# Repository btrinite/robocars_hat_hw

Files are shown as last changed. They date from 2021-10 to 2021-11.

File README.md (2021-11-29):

# This repository contains the hardware part of the DIYRobocarsFr Hat.

## Intro
This Hat is designed for Raspberry Pi 3/4, Jetson Nano or any other SBC implementing the well known 'rpi' GPIO connector.
This Hat provides various interfaces between SBC (Single Board Controler) and hardware to easely build an autonomous small scale RC-style car.
A typical example of such build is the [Donkey car](https://www.donkeycar.com/)

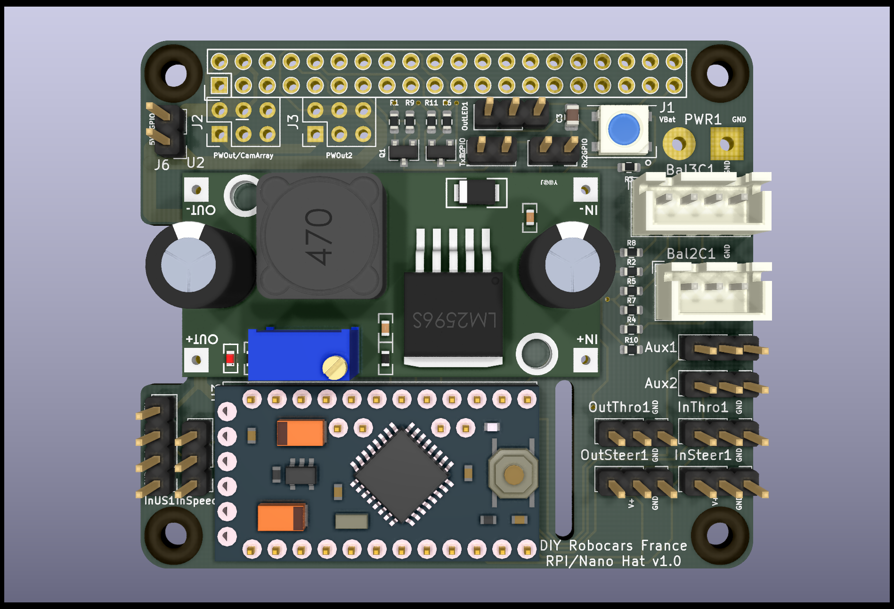
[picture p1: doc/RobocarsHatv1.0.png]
DIY Robocars FR Hat


The Hat combines :
- LM2596 or xl4005 DSN5000 based DC/DC converter to power everything from a single battery (7-15V, NiMh or LiPo 2S/3S), through GPIO or through dedicated connector.
- Arduino pro mini 5V 16Mhz, which drive I/O (PWM Inpput/output, Ultrasonic sensor, RPM sensor, ...). 5V version is prefered since most of the sensors works at 5v.
- Serial communication link between Arduino and SBC through GPIO pin 8 and 10, with level shift 5v/3.3V 
- Tension divider bridge for Battery monitoring
- RBG Led to display status
- compatibility (stackable) with Arducam CamArray

The Hat has the following I/O :
- 40 pin header GPIO compatible with Raspberry PI and Nvidia Jetson with UART0 wired to the arduino through level shift
- 3 Battery power in connectors (2 wires, 3 wires or 4 wires)
- 2 PWM Inputss to connect RC Receiver (Throttle and Steering input)
- 2 PWM Outputs to connect drive train (ESC and Servo, for Throttle and Steering output) 
- 2 PWM Aux Inputs/Outputs
- 1 input for RPM sensor
- 1 input for UltraSOund sensor
- Aux connector for additional power output (5V and 3.3V) and to stack ArduCam CamArray
- WS2812B compatible output to control more RGB Led

The follwing jumpers are provided for convenience :
- 5V to GPIO : to inject 5V power supply to the Host through GPIO connector (to power Raspberry or Jetson Nano from the main Battery).
For other Hosts, please check documentation
- UART0 RX/TX Jumper : Usually, you need those jumpers since all communication between Host and Hat goes through this UART. Removing those jumpers could be needed to isolate Arduino UART while re-flashing it (especially if Host is powered on at flahsing time).

## Wiring
A typical wiring of the Hat is shown below : 

Hat Wiring

## Schematic

Consult [Schematics.pdf](doc/Schematics.pdf)

## Note on PWM Block

### Power supply
Hat does not provide power supply through PWM Inputs/Outpus. It is usualy duty of the motor controller (ESC) which feature a BEC.
This is to avoid mixing logic and actuators on the same power source. It means that as long as ESC is not connected and switchded on, Servo and RX Receiver will not be powered.

### output Idle signal
In the current implementation,

- First, as soon as the Hat is powered, a default Idle signal is driven (1,5ms pulse width)
This default idle signal could differ from the one you could have when doing calibration. 

- Second, many ESC will autocalibrate to this idle signal at startup time (when switched on) 

If you are in that case, it is recommanded to switch on the ESC only after the main application is up and running.

## Dependencies

Third party components libraries needed :

* [LM2596 DC to DC buck/step-down module](https://github.com/yet-another-average-joe/KiCad-Chinese_Modules/tree/main/DCDC_StepDown_LM2596)

* https://github.com/g200kg/kicad-lib-arduino.git

## Firmware

### Source
Firmware to upload to the Arduino ca be found [here](https://github.com/btrinite/robocars_hat)

### Flash firmware
To flash firmware, you need to connect a 5V FTDI adaptor featuring DTR signal and use Arduino IDE to flash/upload the content.
Do not forget to solder Pin header connector on Arduino Pins dedicated for uploading/flash purpose.
You can find more informations [here](https://www.arduino.cc/en/Guide/ArduinoProMini)

## Troubleshooting

### Loopback test (only applicable when using SimpleSerial protocol version of the firmware)
SimpleSerial protocol messages that carry throttle and steering are almost symetrical. Thus, if you loopback the serial comunication (RX wired to TX), the Hat will
work in loopback mode. Throttle/Steering orders received from RX Receiver will be used to drive Throttle/Steering output.

Loopback mode is achieved by :
- removing Rx/Tx jumpers to decouple UART signal from Host
- Wiring Rx and Tx together

This is illsutrated below : 

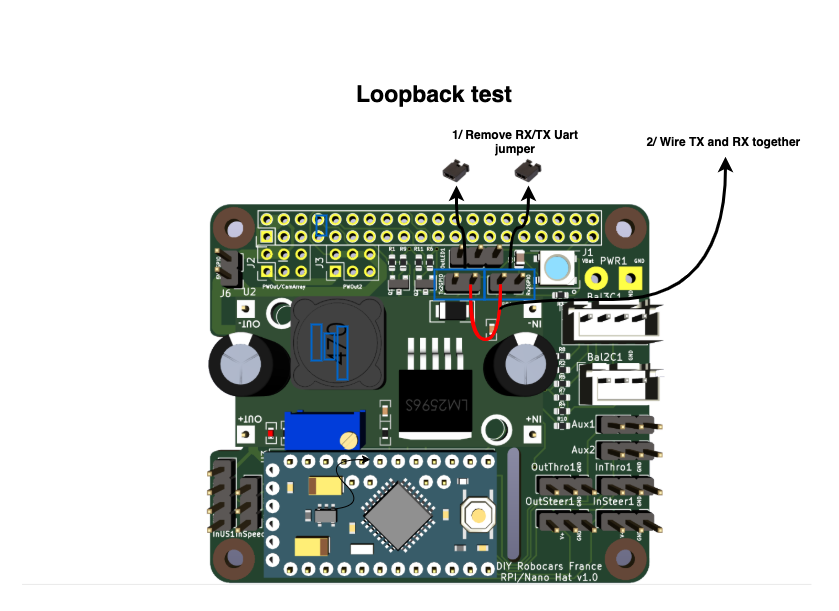
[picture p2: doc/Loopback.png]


## Example of integration
Modified Donkeycar software with integration of the DIYRobocarsFr Hat is available [here](https://github.com/btrinite/donkey_with_robocars_hat)

## Credits
Based on https://github.com/devbisme/RPi_Hat_Template

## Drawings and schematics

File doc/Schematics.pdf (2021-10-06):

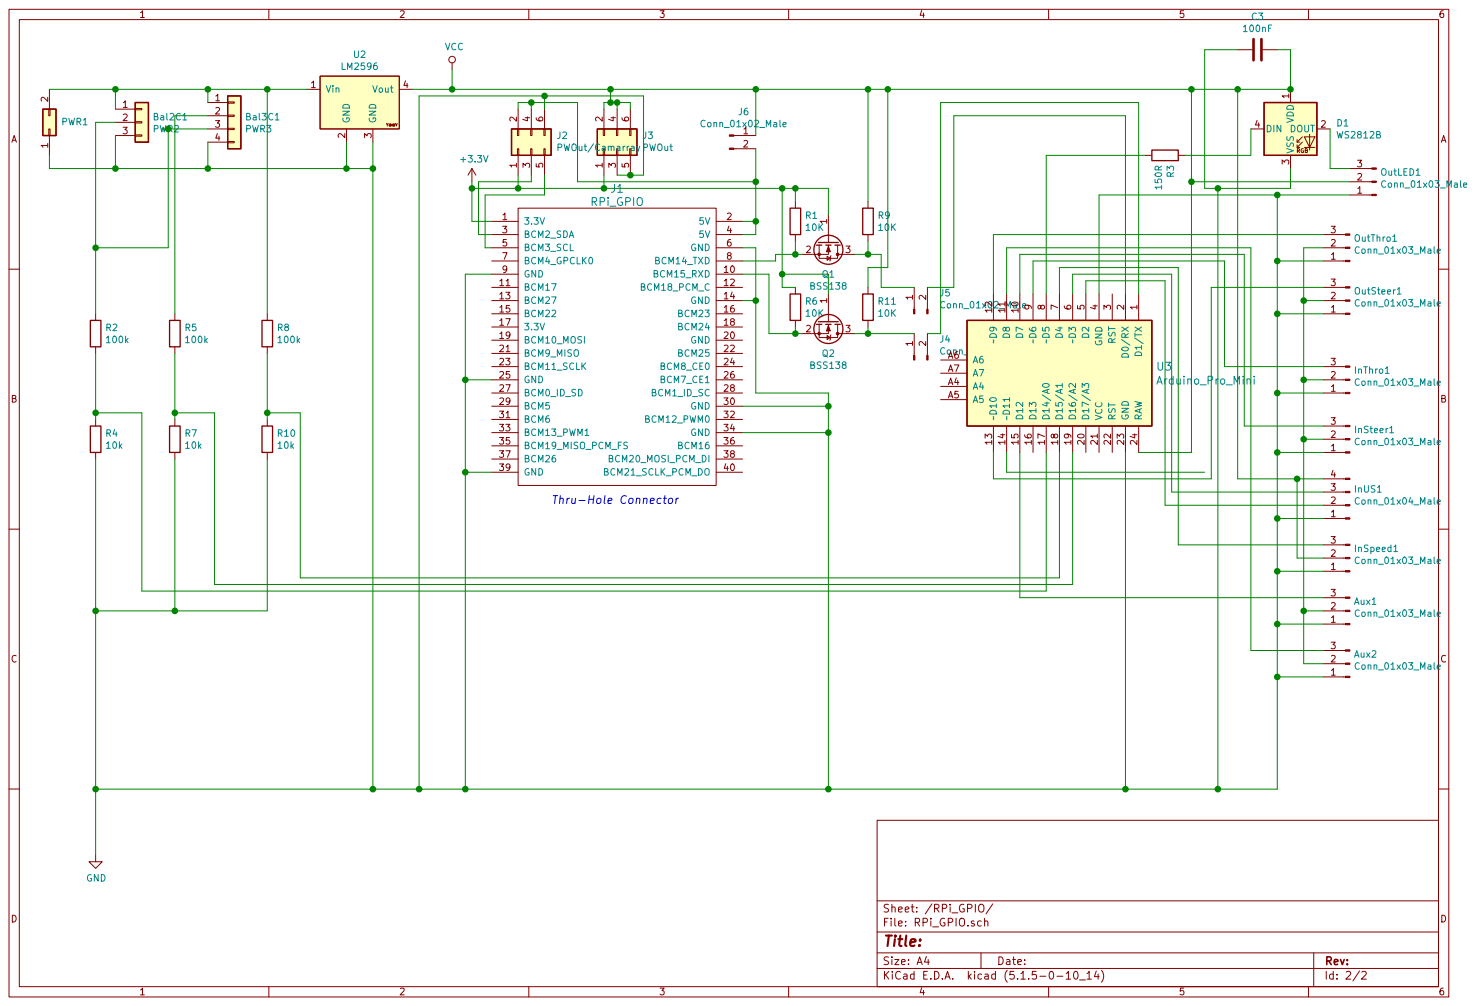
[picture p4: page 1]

2 D17/A3 20 VCC 21 RST 22 GND 23 RAW 24 RST

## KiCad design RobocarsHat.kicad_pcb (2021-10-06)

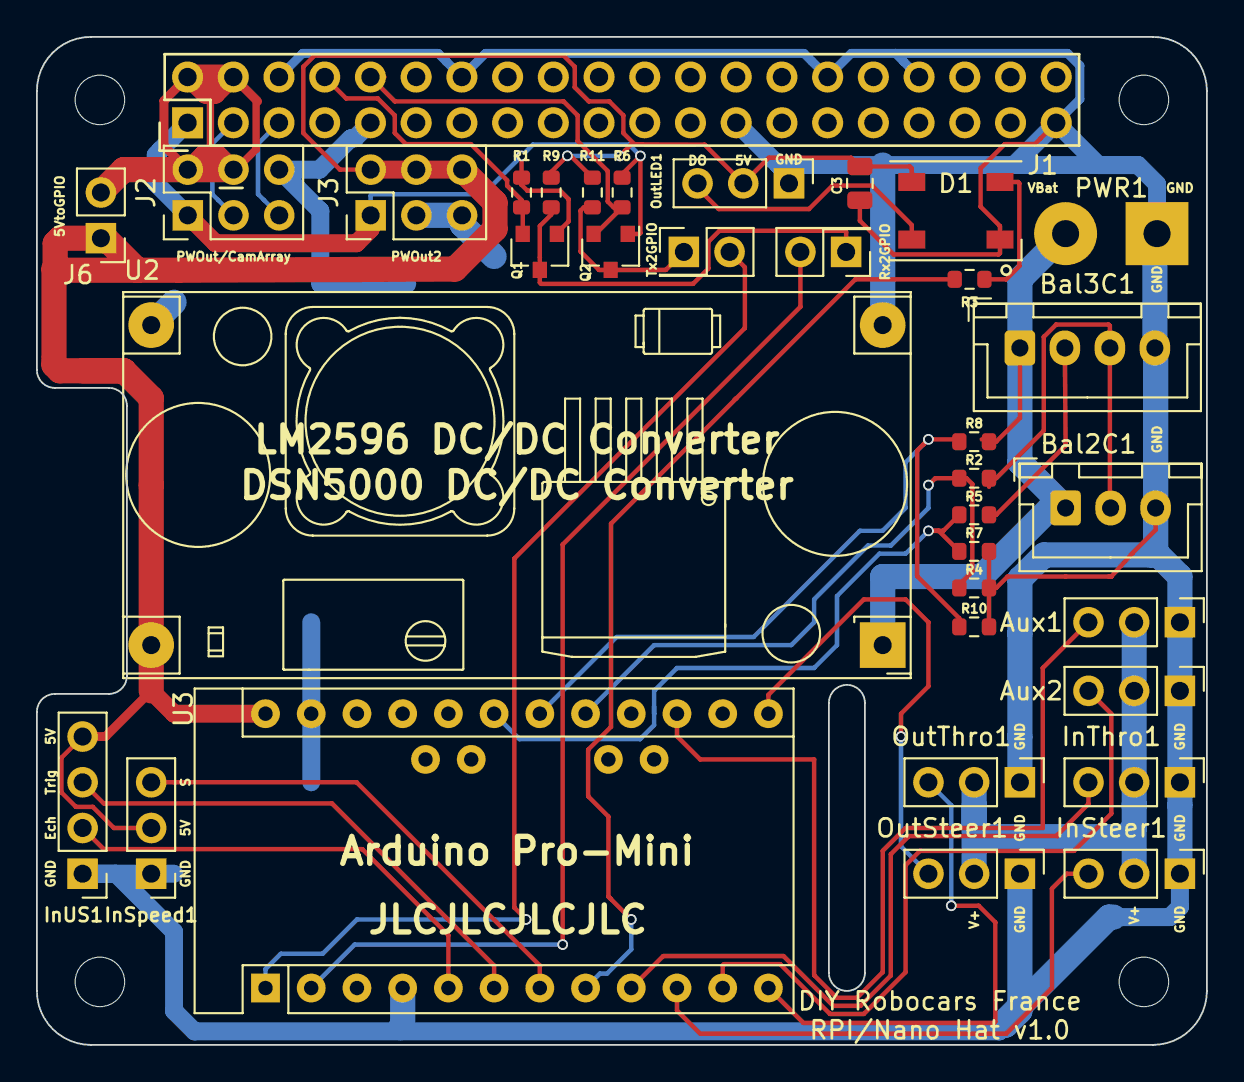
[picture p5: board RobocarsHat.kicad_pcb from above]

Board: 2 copper layers, 65.0 x 56.0 mm, 35 parts (0 on the bottom side), 31 nets.

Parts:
Aux1, Aux2: Conn_01x03_Male; PinHeader_1x03_P2.54mm_Vertical
Bal2C1: PWR2; JST_XH_B3B-XH-A_1x03_P2.50mm_Vertical
Bal3C1: PWR3; JST_XH_B4B-XH-A_1x04_P2.50mm_Vertical
C3: 100nF; C_0805_2012Metric
D1: WS2812B; LED_WS2812B_PLCC4_5.0x5.0mm_P3.2mm
InSpeed1: Conn_01x03_Male; PinHeader_1x03_P2.54mm_Vertical
InSteer1: Conn_01x03_Male; PinHeader_1x03_P2.54mm_Vertical
InThro1: Conn_01x03_Male; PinHeader_1x03_P2.54mm_Vertical
InUS1: Conn_01x04_Male; PinHeader_1x04_P2.54mm_Vertical
J1: RPi_GPIO; Pin_Header_Straight_2x20
J2: PWOut/Camarray; Pin_Header_Straight_2x03_Pitch2.54mm
J3: PWOut; Pin_Header_Straight_2x03_Pitch2.54mm
J4, J5: Conn_01x02_Male; PinHeader_2x01_P2.54mm_Vertical
J6: Conn_01x02_Male; PinHeader_1x02_P2.54mm_Vertical
OutLED1: Conn_01x03_Male; PinHeader_1x03_P2.54mm_Vertical
OutSteer1: Conn_01x03_Male; PinHeader_1x03_P2.54mm_Vertical
OutThro1: Conn_01x03_Male; PinHeader_1x03_P2.54mm_Vertical
PWR1: PWR1; SolderWirePad_1x02_P5.08mm_Drill1.5mm
Q1, Q2: BSS138; SOT-23
R1, R6, R9, R11: 10K; R_0603_1608Metric
R2, R5, R8: 100k; R_0603_1608Metric
R3: 150R; R_0603_1608Metric
R4, R7, R10: 10k; R_0603_1608Metric
U2: LM2596; YAAJ_DCDC_StepDown_LM2596
U3: Arduino_Pro_Mini

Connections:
+3V3: J1.1, J2.1, J3.1, Q1.1, Q2.1, R1.1, R6.1
GND: Aux1.1, Aux2.1, Bal2C1.3, Bal3C1.4, C3.2, D1.3, InSpeed1.1, InSteer1.1, InThro1.1, InUS1.1, J1.6, J1.9, J1.14, J1.25, J1.30, J1.34, J1.39, J2.6, J3.3, J3.5, OutLED1.1, OutSteer1.1, OutThro1.1, PWR1.1, R4.2, R7.2, R10.2, U2.2, U2.3, U3.4, U3.23
unnamed: Aux1.2, Aux2.2, InSteer1.2, InThro1.2, OutSteer1.2, OutThro1.2
unnamed: Aux1.3, U3.15
unnamed: Aux2.3, U3.11
unnamed: Bal2C1.1, Bal3C1.1, PWR1.2, R8.1, U2.1
unnamed: Bal2C1.2, Bal3C1.3, R2.1
unnamed: Bal3C1.2, R5.1
unnamed: D1.2, OutLED1.3
unnamed: D1.4, R3.1
unnamed: InSpeed1.3, U3.7
unnamed: InSteer1.3, U3.10
unnamed: InThro1.3, U3.9
unnamed: InUS1.2, U3.5
unnamed: InUS1.3, U3.6
unnamed: J1.2, J1.4, J2.2, J2.4, J6.2
unnamed: J1.3, J2.3
unnamed: J1.5, J2.5
unnamed: J1.8, Q1.2, R1.2
unnamed: J1.10, Q2.2, R6.2
unnamed: J4.1, Q2.3, R11.2
unnamed: J4.2, U3.1
unnamed: J5.1, Q1.3, R9.2
unnamed: J5.2, U3.2
unnamed: OutSteer1.3, U3.13
unnamed: OutThro1.3, U3.12
unnamed: R2.2, R4.1, U3.17
unnamed: R3.2, U3.8
unnamed: R5.2, R7.1, U3.19
unnamed: R8.2, R10.1, U3.18
VCC: C3.1, D1.1, InSpeed1.2, InUS1.4, J3.2, J3.4, J3.6, J6.1, OutLED1.2, R9.1, R11.1, U2.4, U3.24

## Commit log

2021-10-21 readme + bom
2021-10-28 note on PWM
